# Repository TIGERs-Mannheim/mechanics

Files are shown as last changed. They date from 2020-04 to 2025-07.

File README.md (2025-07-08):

# TIGERs Mannheim Open-Source Mechanics

This repository contains mechanics for our robots and our base station. There is one folder for each released version.  
Mechanics are designed with: 
 - [Autodesk Inventor Professional 2019](https://www.autodesk.com/education/free-software/inventor-professional) (v2020) 
 - [Autodesk Inventor Professional 2022](https://www.autodesk.com/education/free-software/inventor-professional) (v2022) 
 - [Autodesk Inventor Professional 2023](https://www.autodesk.com/education/free-software/inventor-professional) (v2023, v2024, v2025) 
 
Autodesk Inventor is available for free for students.

Have a look at our [2020 ETDP](https://tigers-mannheim.de/download/tdps/2020_ETDP_TIGERS.pdf) and [2020 Champion Paper](https://download.tigers-mannheim.de/papers/2021-RoboCup-Champion.pdf) which contain many details about design decisions and lessons learned over more than 10 years.

Please check subfolders for further information on each version.

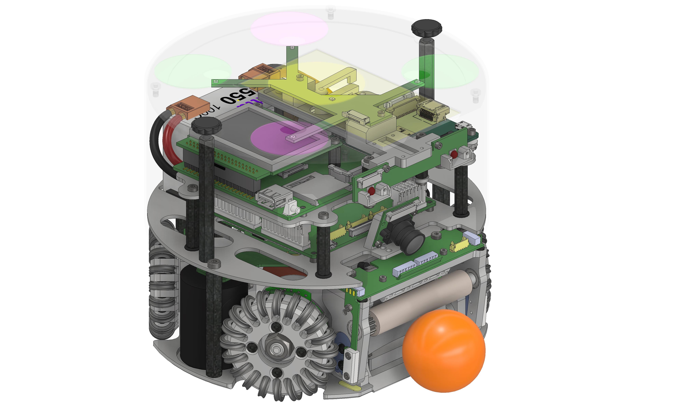
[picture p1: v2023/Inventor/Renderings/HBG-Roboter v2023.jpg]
v2023 Robot


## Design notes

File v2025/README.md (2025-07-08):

# v2025 Mechanics

Compared to the v2024 release the following changes have been made:
- The robot case for the black and white hull requirement has been redesigned
- The rear and side dribbler dampers have been updated in shape
- Camera and ball sensor arrays have been removed

Inventor folder contains the complete Inventor project for robot and base station including all parts.

STEP folder contains full step files of the robot assembly and the base station assembly. These files should be compatible with most CAD programs.

The `Purchased Parts.xlsx` file lists all third-party components used in the robot, including quantities, online shop URL and order number.  

## Electronic boards
v2025 robots use the following electronics boards which can be found in the electronics open-source repo:
- Ball Detection v4 (Break beam sensor)
- Encoder iC-PX v1b (Encoder IC carrier board)
- Front LEDs v1b
- IR Controller v2 (Break beam processor)
- Kicking Device v13b (Capacitor charge/discharge board)
- Mainboard v13 (Primary microcontroller and wireless transmitter board)
- Pattern Ident v2 (Automatic pattern identification system)
- Powerboard v1 (High current power board, motor controllers and power distribution)

## Inventor
To make sure all parts can be found by Inventor open the corresponding project file under `Inventor/TIGERs 2025.ipj`.  
The primary assembly file for the robot is `Inventor/Robot/HBG-Roboter v2025.iam`. You can open sub-assemblies by right-clicking on them and select open.  
The primary assembly file for the base station is `Inventor/Base Station/HBG-Base Station v3.iam`.

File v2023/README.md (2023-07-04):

# v2023 Mechanics

Compared to the v2022 release changes have been made to the dribbler dampening mechanism. Furthermore, dampers and dribbling bar are now 3D printed and part of the STL files. The sub-wheel axes of all wheels have been changed to better fit in the main wheel pockets.

Inventor folder contains the complete Inventor project for robot and base station including all parts.

PDF folder contains manufacturing drawings for parts produced by milling or turning. Note that only outer dimensions and important tolerances are given. Other data must be taken from STEP files.

STEP folder contains STEP files for manufacturing of parts produced by milling and turning as well as a file for the whole assembly of the robot.

STL folder contains all parts manufactured by 3D printing. See subfolder for material recommendations.

## Electronic boards
v2023 robots use the following electronics boards which can be found in the electronics open-source repo:
- Ball Detection v4 (Break beam sensor)
- Encoder iC-PX v1b (Encoder IC carrier board)
- Front LEDs v1b
- IR Controller v2 (Additional ball sensor and break beam processor)
- Kicking Device v13b (Capacitor charge/discharge board)
- Mainboard v13 (Primary microcontroller and wireless transmitter board)
- Pattern Ident v2 (Automatic pattern identification system)
- Powerboard v1 (High current power board, motor controllers and power distribution)

## Inventor
To make sure all parts can be found by Inventor open the corresponding project file under `Inventor/TIGERs 2023.ipj`.  
The primary assembly file for the robot is `Inventor/Robot/HBG-Roboter v2023.iam`. You can open sub-assemblies by right-clicking on them and select open.  
The primary assembly file for the base station is `Inventor/Base Station/HBG-Base Station v3.iam`.  
The excel list at `Inventor/Purchased Parts.xlsx` contains all purchased parts, including quantities, online shop URL and order number.  
Some image renderings are available at `Inventor/Renderings`.  
Inventor presentation files and drawings are in `Inventor/Presentations` and `Inventor/Drawings`, respectively.

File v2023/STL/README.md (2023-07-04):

# 3D Printed-Parts

All parts have been successfully printed on a Prusa i3 MK3S printer with a standard 0.4mm nozzle.
File names correspond to Inventor part names.

### Base Station v3
Recommended materials and layer heights for each part:

| Part | Material | Layer Height |
| --- | --- | --- |
| Base Station v3 | PLA | 0.2mm |

### Robot
Recommended materials and layer heights for each part:

| Part | Material | Layer Height |
| --- | --- | --- |
| Akkuhalter | PLA | 0.2mm |
| Akkusperre | PETG | 0.2mm |
| Akkusperre Klein | PETG | 0.2mm |
| Ballsensor Platinenwinkel | PLA | 0.1mm |
| Ballsensormaske | PLA | 0.1mm |
| Chipanschlag L2.0 | TPU98 | 0.1mm |
| Displayhalter Bot | PLA | 0.2mm |
| Dribbler Slider | Recreus FilaFlex 70A | 0.2mm |
| Dribbler Slider gespiegelt | Recreus FilaFlex 70A | 0.2mm |
| Dribblerschnecke v2 | Recreus FilaFlex 70A | 0.2mm |
| Dribblerdaempfer v2 | Recreus FilaFlex 70A | 0.2mm |
| Gehäuse Mantel | PETG | 0.3mm |
| Gehäuse Unterplatte | PLA | 0.2mm |
| IR Schutz | PLA | 0.2mm |
| Kamerahalter Vorne geneight | PLA | 0.2mm |
| Kameraplatte | PLA | 0.2mm |
| Kickerboard Winkel | PLA | 0.2mm |
| Kickerdaempfer | TPU98 | 0.2mm |
| LED Schirm | PETG | 0.2mm |
| Spulenkörper | PLA | 0.2mm |

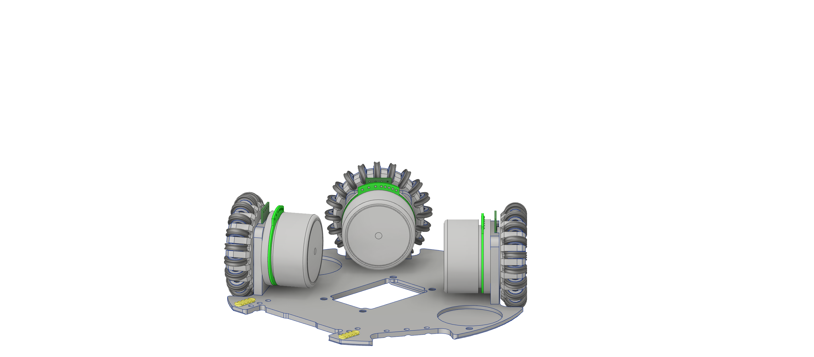
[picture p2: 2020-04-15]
v2020/Inventor/Renderings/HBG-Roboter v2020-5.png

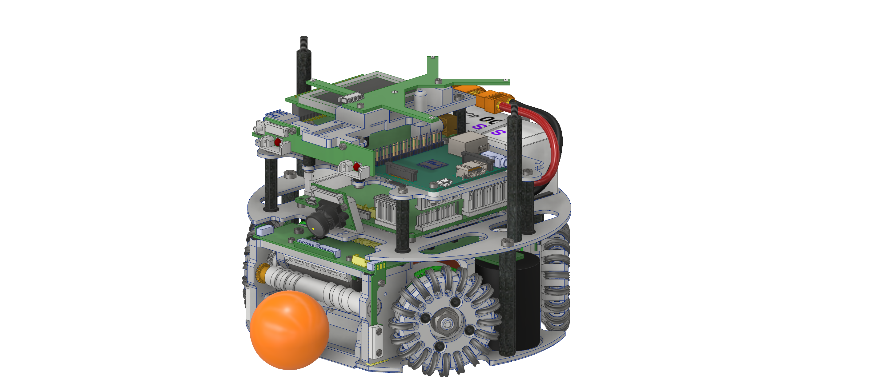
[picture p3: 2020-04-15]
v2020/Inventor/Renderings/HBG-Roboter v2020-1.png

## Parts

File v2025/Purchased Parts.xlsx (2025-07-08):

Quantity | Part | Description | Supplier | Part Number
8 | ISO 1580 M2 x 3 | Flachkopfschraube mit Schlitz, rostfrei | wegertseder.de | 1094-002
4 | DIN 84 - M3 x 6 | Zylinderschraube, polyamid schwarz | wegertseder.de | 3989-300
4 | ISO 4762 - M2 x 4 | Zylinderschraube | wegertseder.de | 2534-230
34 | ISO 4762 - M2 x 6 | Zylinderschraube | wegertseder.de | 2534-234
4 | ISO 4762 - M2,5 x 10 | Zylinderschraube | wegertseder.de | 2534-258
28 | DIN 7984 - M3 x 5 | Zylinderschraube, rostfrei | wegertseder.de | 2594-928
10 | DIN 7984 - M4 x 6 | Zylinderschraube, niedriger Kopf | wegertseder.de | 2594-954
20 | ISO 10642 - M3 x 6 | Senkschraube mit Innensechskant | wegertseder.de | 2608-680
42 | ISO 10642 - M3 x 8 | Senkschraube mit Innensechskant | wegertseder.de | 2608-682
8 | ISO 10642 - M4 x 8 | Senkschraube mit Innensechskant | wegertseder.de | 2608-708
2 | DIN 467 - M4 | Rändelmutter M4 | wegertseder.de | 2058-782
4 | DIN 934 - M2,5 | Sechskantmuttern, M2.5 | wegertseder.de | 2896-142
4 | DIN 934 - M8 | Sechskantmuttern, Alu, M8 | wegertseder.de | 2914-422
4 | DIN 562 M3 | Vierkantmutter, niedrige Form, M3 | wegertseder.de | 3198-486
0 | DIN 125 A3.2 | Unterlegscheibe, polyamid | wegertseder.de | 1504-436
0 | DIN 125 A5.3 | Unterlegscheibe, polyamid | wegertseder.de | 1504-440
4 | DIN 137 B8 | Federscheibe Form B, 8mm, Federstahl, verzinkt | wegertseder.de | 1738-294
10 | ISO 2338 - 2 m6 x 4 | Zylinderstift m6 2x4 | wegertseder.de | 4347-136
80 | ISO 2338 - 2 m6 x 6 | Zylinderstift m6 2x6 | wegertseder.de | 4347-140
1 | ISO 2338 - 2 m6 x 16 | Zylinderstift m6 2x16 | wegertseder.de | 4347-150
0 | DIN 988 4 x 8 x 0,2 | Passscheibe M4, 0.2mm | wegertseder.de | 1652-940
4 | DIN EN ISO 8745 4 x 10 | Paßkerbstift 4x10 | wegertseder.de | 1028-042
1 | Moons ECU22048H18 | Moons ECU22048H18, 55W, 18V, Slotless BLDC Motor | moonsindustries.com | ECU22048H18-S101
4 | DF45L024048-A2 | Motor Nanotec, 65Watt, 24V | nanotec.de | DF45L024048-A2
4 | iC-PX2604 | iC-PX2604 oDFN8-3x3 Reflective Encoder, 23040cpr | ichaus.de | iC-PX2604
4 | PX01FS | PX01FS 26-360 Code Disc, 360, selbstklebend | ichaus.de | PX01FS 26-360
1 | Akku 6S1P Tattu | Tattu Funfly 1550mAh 22,2V 100C | gensace.de | TAA15506S10X6
1 | XT Akku Anschluss | XT60 Stecker | stefansliposhop.de | SLS XT-60 Stecker SK
1 | Charge Marker | Charge Marker | stefansliposhop.de | C-Marker
2 | Kugellager 685-ZZ-C3 | Kugellager, beidseitig Deckscheiben, ID=5, AD=11, b=5 | kugellager-express.de | 685-ZZ-C3
2 | Kugellager 683-ZZ | Kugellager, beidseitig Deckscheiben, ID=3, AD=7, b=3 | kugellager-express.de | 683-ZZ
2 | Zahnrad z14 Modul 0.7 | Stirnzahnrad, Stahl, Modul 0.7, z=14 | maedler.de | 21201400
1 | Zahnrad Polyketon z16 Modul 0.7 | Stirnzahnrad, Polyketon, Modul 0.7, z=16 | maedler.de | 28201601
80 | X-Ring, 5.94x3.53 | X-Ring, 5.94x3.53mm, NBR, Shore A 70 | ir-dichtungstechnik.de | XRINGBS202NBR70
160 | Gleitlager MSM-0205-02 | Gleitlager Querrolle MSM-0205-02 | igus.de | JSM-1012-05
4 | Zugfeder Z-015LI | Zugfeder Z-015LI, Kicker | federnshop.com | Z-015LI
2 | Zugfeder RZ-006DI | Zugfeder RZ-006DI, Chip Schaufel | federnshop.com | RZ-006DI
4 | M4x60 | Abstandsbolzen Typ A, M4, 60mm, Kunststoff | ettinger.de | 5.30.460
2 | M4x70 | Abstandsbolzen Typ B, M4, 70mm, Stahl | ettinger.de | 5.14.701
4 | M3x30 | Abstandsbolzen Typ A, M3, 30mm, Kunststoff | ettinger.de | 5.30.330
3 | M3x20 | Abstandsbolzen Typ A, M3, 20mm, Kunststoff | ettinger.de | 5.30.320
28 | Kupferlackdraht 140m | Kupferlackdraht (Spule) 0.63mm, 6-7 Lagen | conrad.de | 605523
 |  | Doppelseitiges Klebeband, schneidbar | conrad.de | 542373
8 |  | Gummitülle 3mm | digikey.de | 1722-1291-ND
4 |  | Distanzhülse 3mm M2.5 (RPi) | digikey.de | 952-1526-ND
2 |  | Abstandsbolzen Kunststoff (Mainboard), 12mm | digikey.de | 952-3457-ND
 | Loctite | Wellensicherungskleber im Spenderstift | de.rs-online.com | 476-7870

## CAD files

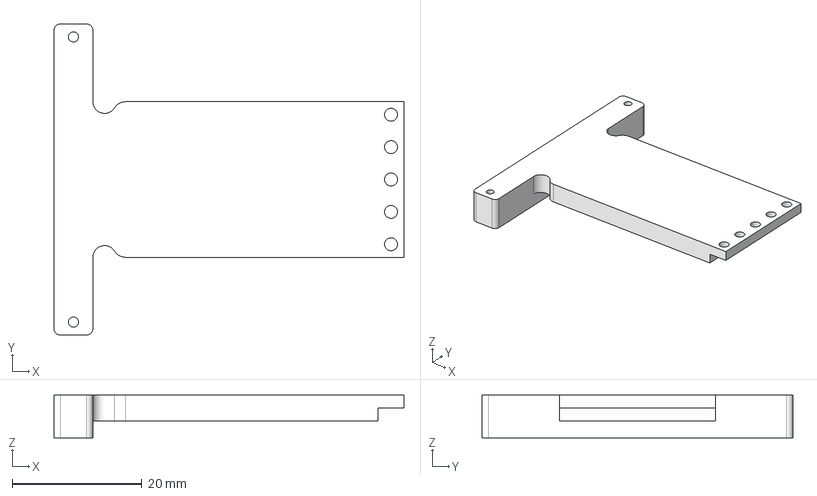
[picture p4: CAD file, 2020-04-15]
v2020/STEP/32_Kicker Chip.ipt.step
54.0 x 48.0 x 6.60 mm

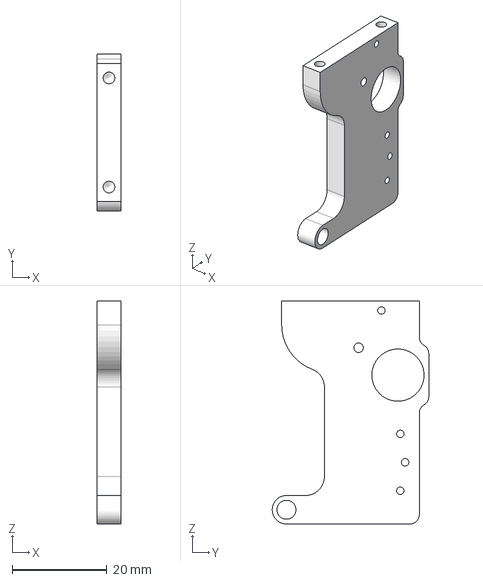
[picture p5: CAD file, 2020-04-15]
v2022/STEP/21_Dribbler Seite.ipt.step
5.00 x 33.0 x 47.0 mm

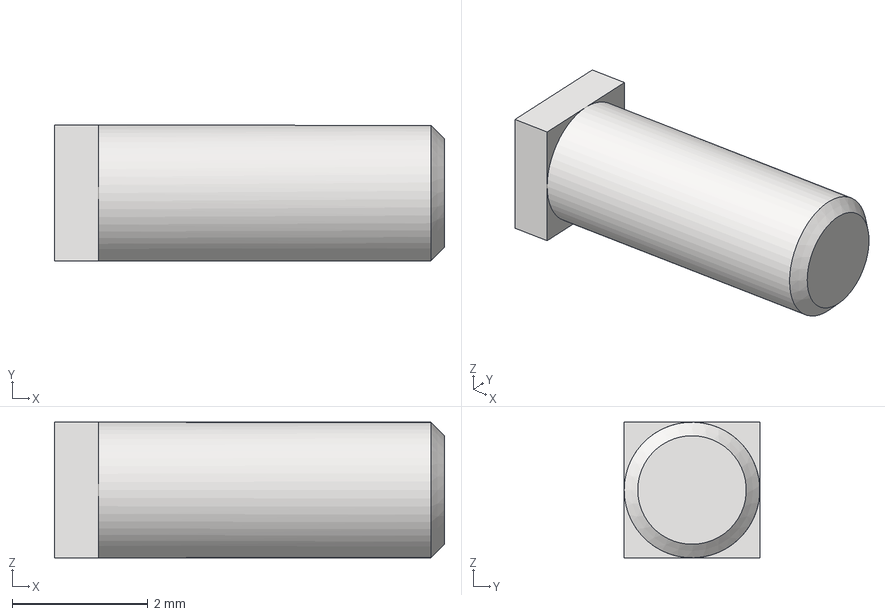
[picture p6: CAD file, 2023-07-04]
v2023/STEP/16_Welle Querrolle Quad.stp
5.75 x 2.00 x 2.00 mm

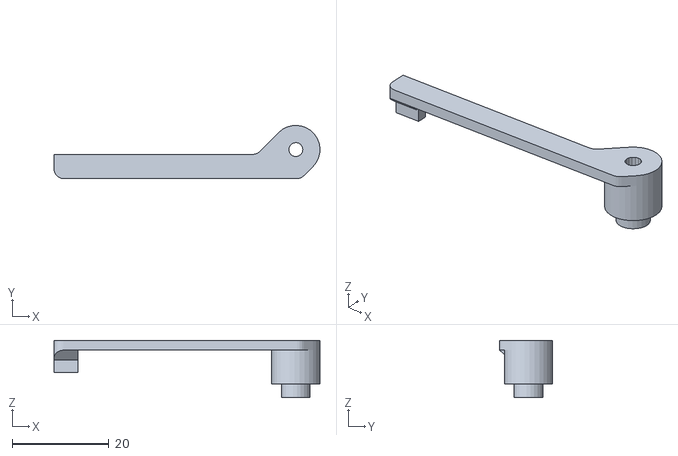
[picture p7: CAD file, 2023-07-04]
v2023/STL/Robot/Akkusperre.stl
55.0 x 11.0 x 11.8

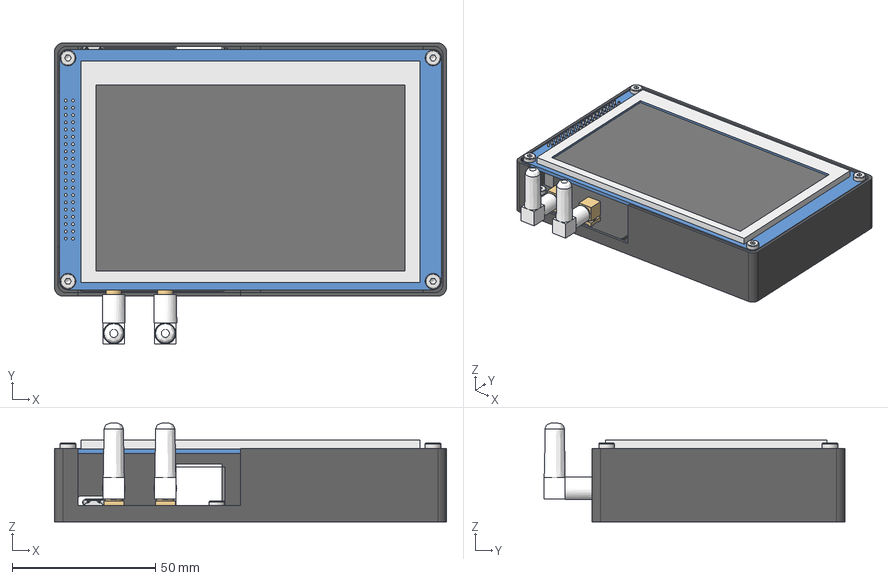
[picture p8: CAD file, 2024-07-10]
v2025/STEP/HBG-Base Station v3.stp
136.9 x 105.1 x 34.4 mm
Gehaeuse BS v3
Base Station PCB
RJ45 Socket
Antenne-Klein x 2
SMA-F-RA x 2
ESQ-120-33-T-D_socket
ESQ-120-33-T-D_pins
ESQ-120-33-G-D-LL_bpins
TFT-CP11009
DIN 7984 - M3 x 5 x 7

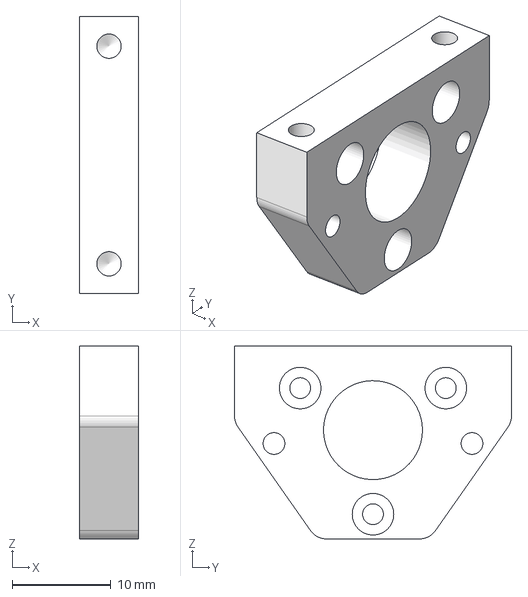
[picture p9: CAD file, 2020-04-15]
v2020/STEP/25_Motorhalter.ipt.step
6.00 x 28.0 x 19.5 mm

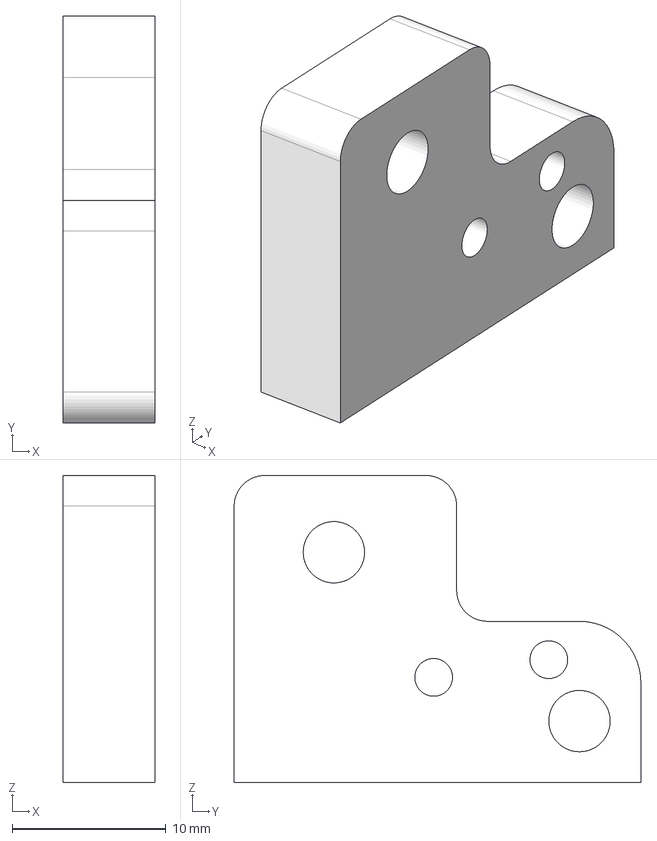
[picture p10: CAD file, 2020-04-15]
v2022/STEP/20_Dribbler Lagerbock.ipt.step
6.00 x 26.5 x 20.0 mm

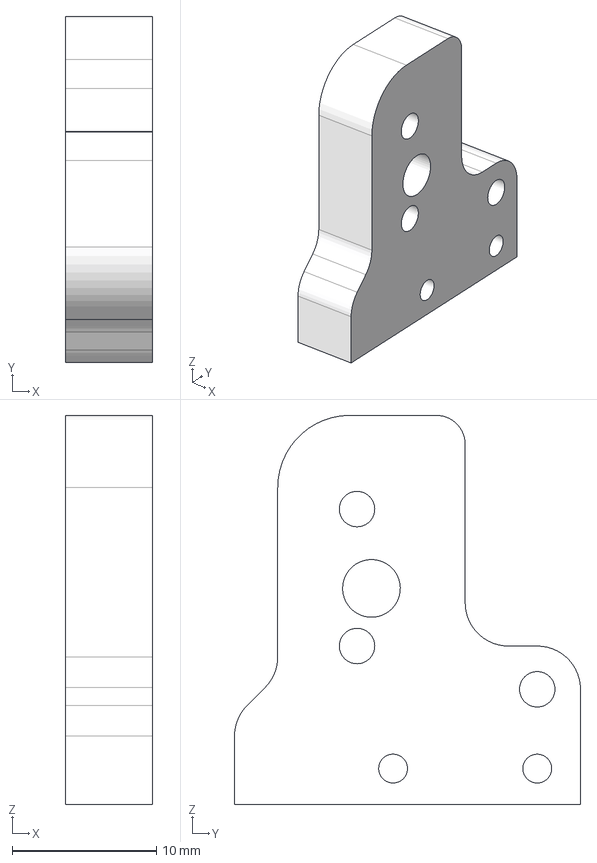
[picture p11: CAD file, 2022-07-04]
v2023/STEP/26D_Dribbler Lagerbock v2.ipt.step
6.00 x 24.0 x 27.0 mm

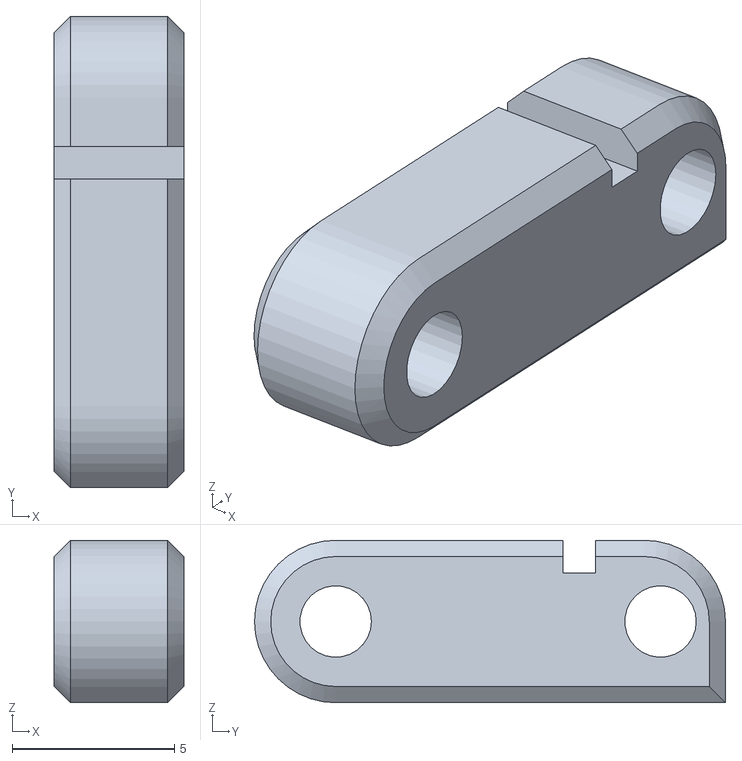
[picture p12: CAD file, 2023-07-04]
v2023/STL/Robot/Chipanschlag L2.0.stl
4.00 x 14.5 x 5.00

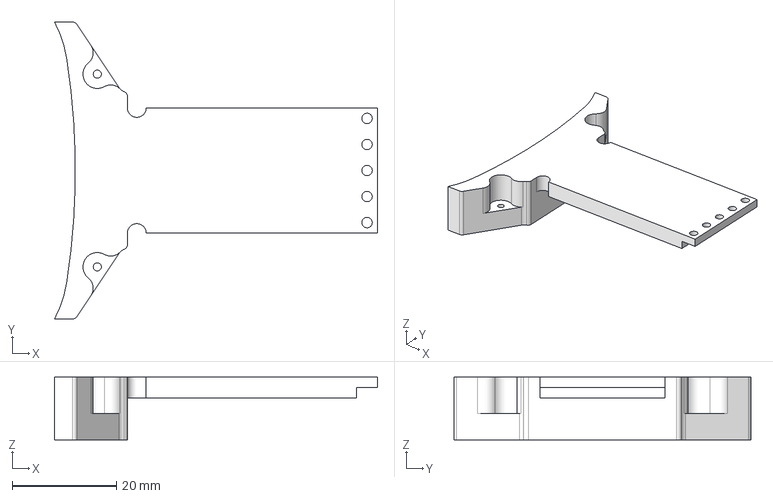
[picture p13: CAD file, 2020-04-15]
v2020/STEP/31_Kicker Sichel.ipt.step
62.0 x 57.0 x 12.0 mm

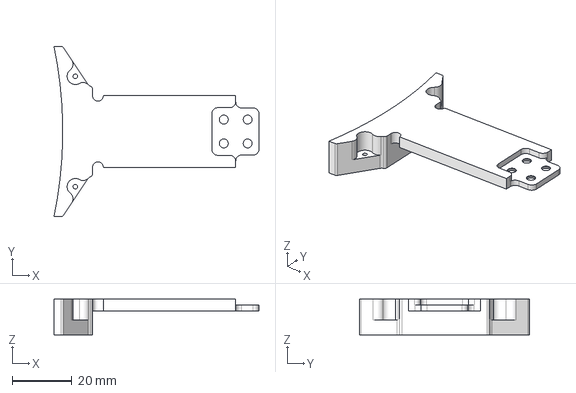
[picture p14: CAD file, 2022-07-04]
v2023/STEP/31B_Kicker Sichel.ipt.step
68.7 x 57.0 x 12.0 mm

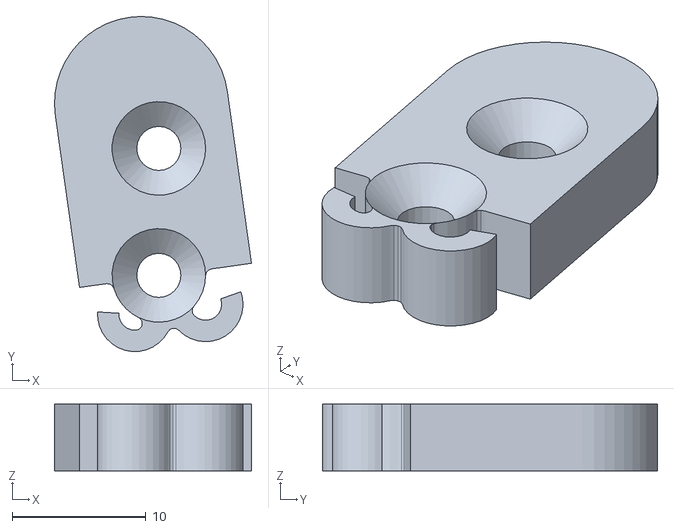
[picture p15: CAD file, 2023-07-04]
v2023/STL/Robot/Dribbler Slider.stl
14.7 x 25.1 x 5.00

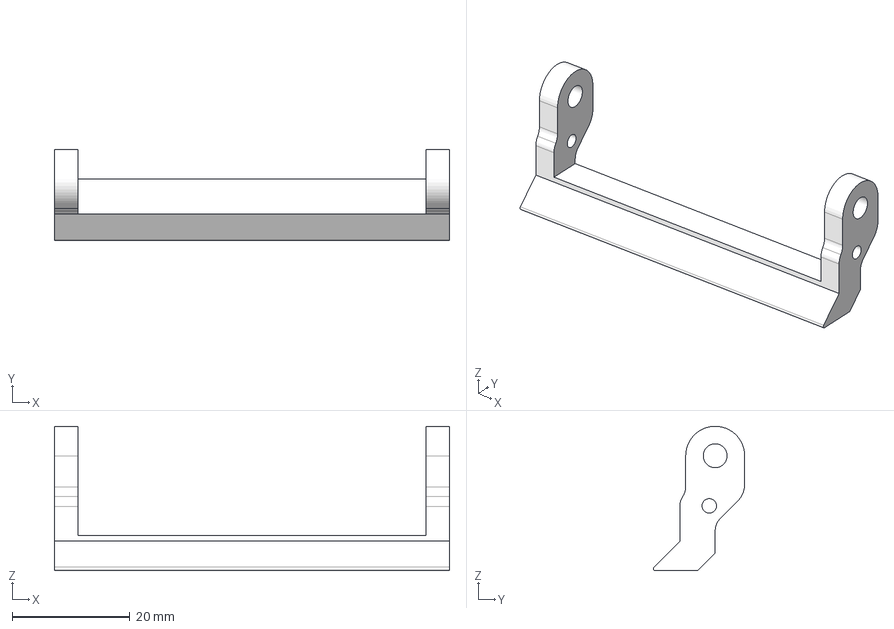
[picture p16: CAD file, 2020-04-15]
v2020/STEP/23_Chip Schaufel.ipt.step
67.0 x 15.5 x 24.5 mm

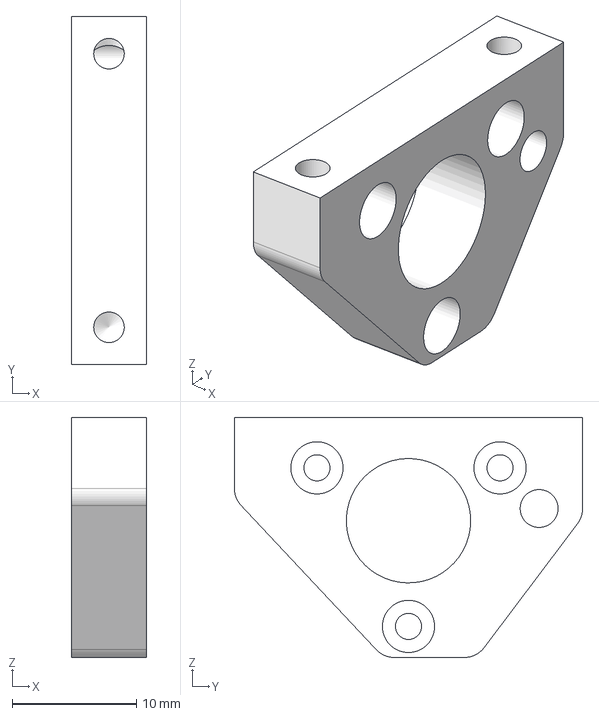
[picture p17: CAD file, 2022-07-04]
v2023/STEP/25D_Motorhalter.ipt.step
6.00 x 28.0 x 19.3 mm

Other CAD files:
v2023/STL/Robot/Akkusperre Klein.stl
v2020/STEP/30_Kicker Eisen.ipt.step
v2023/STEP/30B_Kicker Eisen.ipt.step
v2023/STL/Robot/Dribblerschnecke v2.stl
v2020/Inventor/Base Station/Base Station PCB.ipt
v2020/Inventor/Base Station/Gehaeuse BS v3.ipt
v2020/Inventor/Base Station/HBG-Base Station v3.iam
v2020/Inventor/Base Station/MG-Base Station PCB.iam
v2020/Inventor/Base Station/UBG-Electronics.iam
v2020/Inventor/Drawings/01_Grundplatte.idw
v2020/Inventor/Drawings/02_Mittelplatte.idw
v2020/Inventor/Drawings/03_Oberplatte.idw
v2020/Inventor/Drawings/10_Lagerbock.idw
v2020/Inventor/Drawings/11_Radadapter.idw
v2020/Inventor/Drawings/12_Radkasten.idw
v2020/Inventor/Drawings/13_Raddeckel.idw
v2020/Inventor/Drawings/14_Rolle.idw
v2020/Inventor/Drawings/20_Dribbler Lagerbock.idw
v2020/Inventor/Drawings/21_Dribbler Seite.idw
v2020/Inventor/Drawings/22_Dribbler Bruecke.idw
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

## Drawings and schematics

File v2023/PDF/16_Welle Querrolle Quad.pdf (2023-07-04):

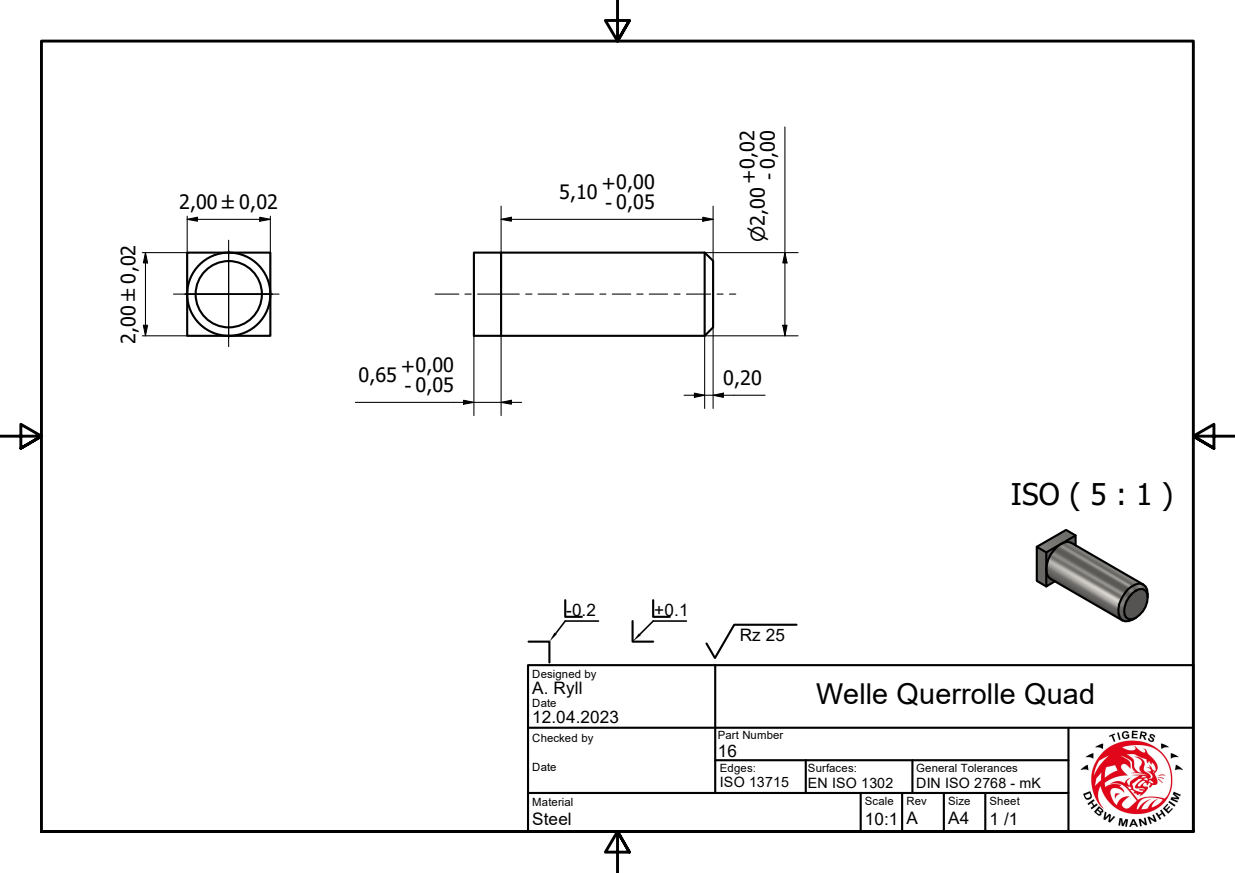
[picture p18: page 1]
ISO ( 5 : 1 )

Designed by A. Ryll Date 12.04.2023 | Welle Querrolle Quad

Checked by Date | Part Number 16

Edges: ISO 13715 | Surfaces: EN ISO 1302 | General Tolerances DIN ISO 2768 - mK

Material Steel | Scale 10:1 | Rev A | Size A4 | Sheet 1 /1

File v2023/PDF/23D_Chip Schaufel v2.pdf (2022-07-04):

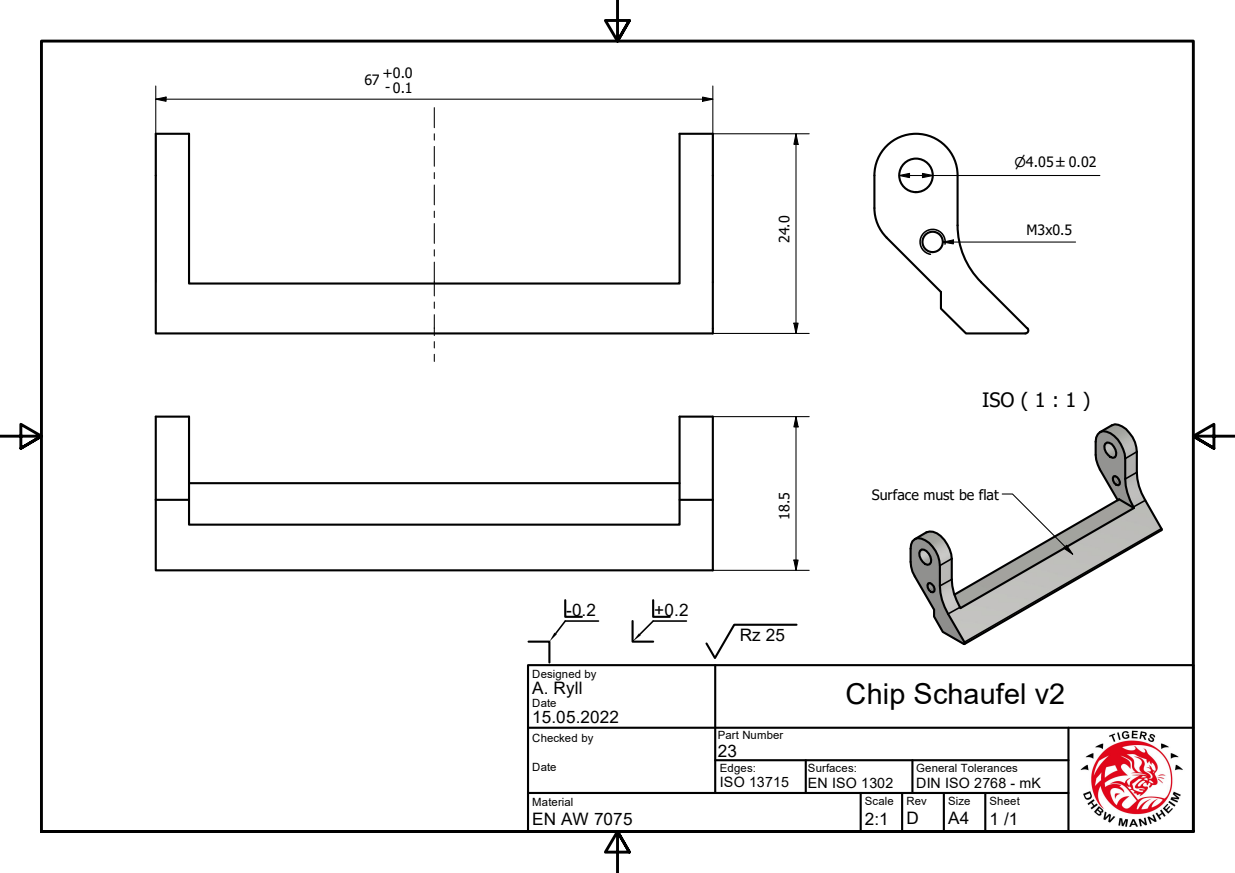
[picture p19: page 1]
ISO ( 1 : 1 )

Surface must be flat

Designed by A. Ryll Date 15.05.2022 | Chip Schaufel v2

Checked by Date | Part Number 23

Edges: ISO 13715 | Surfaces: EN ISO 1302 | General Tolerances DIN ISO 2768 - mK

Material EN AW 7075 | Scale 2:1 | Rev D | Size A4 | Sheet 1 /1

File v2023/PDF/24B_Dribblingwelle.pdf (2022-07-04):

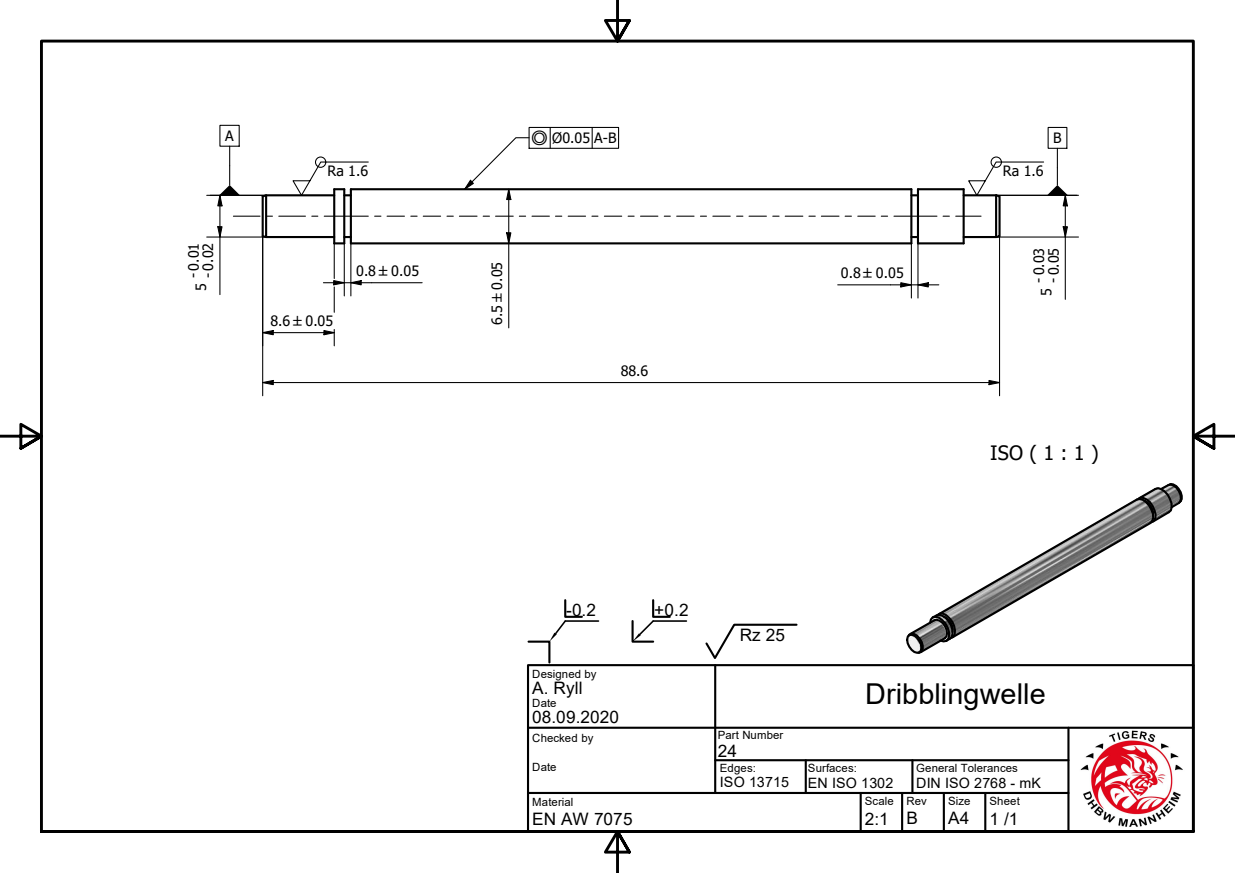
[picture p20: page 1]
ISO ( 1 : 1 )

Designed by A. Ryll Date 08.09.2020 | Dribblingwelle

Checked by Date | Part Number 24

Edges: ISO 13715 | Surfaces: EN ISO 1302 | General Tolerances DIN ISO 2768 - mK

Material EN AW 7075 | Scale 2:1 | Rev B | Size A4 | Sheet 1 /1

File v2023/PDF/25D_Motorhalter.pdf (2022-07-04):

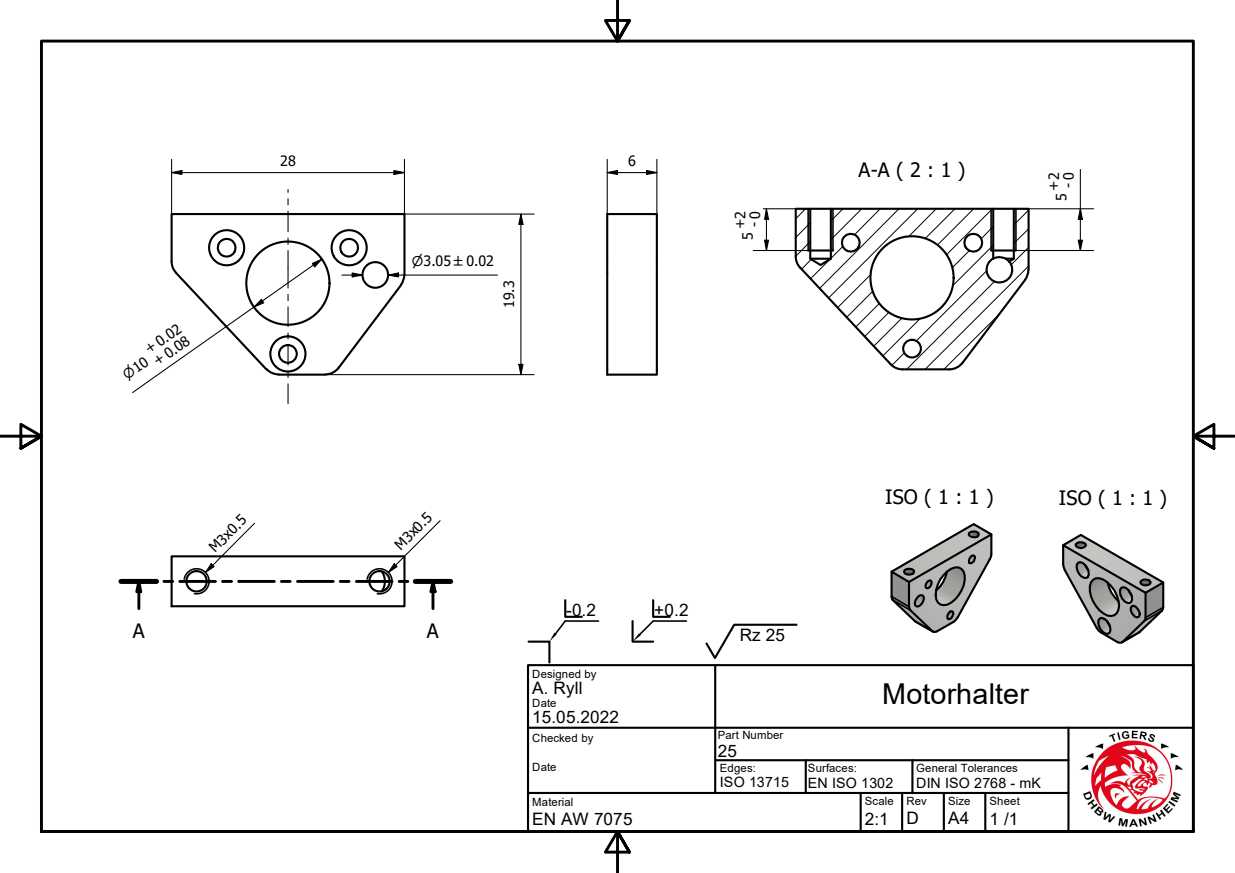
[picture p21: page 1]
ISO ( 1 : 1 )

Designed by A. Ryll Date 15.05.2022 | Motorhalter

Checked by Date | Part Number 25

Edges: ISO 13715 | Surfaces: EN ISO 1302 | General Tolerances DIN ISO 2768 - mK

Material EN AW 7075 | Scale 2:1 | Rev D | Size A4 | Sheet 1 /1

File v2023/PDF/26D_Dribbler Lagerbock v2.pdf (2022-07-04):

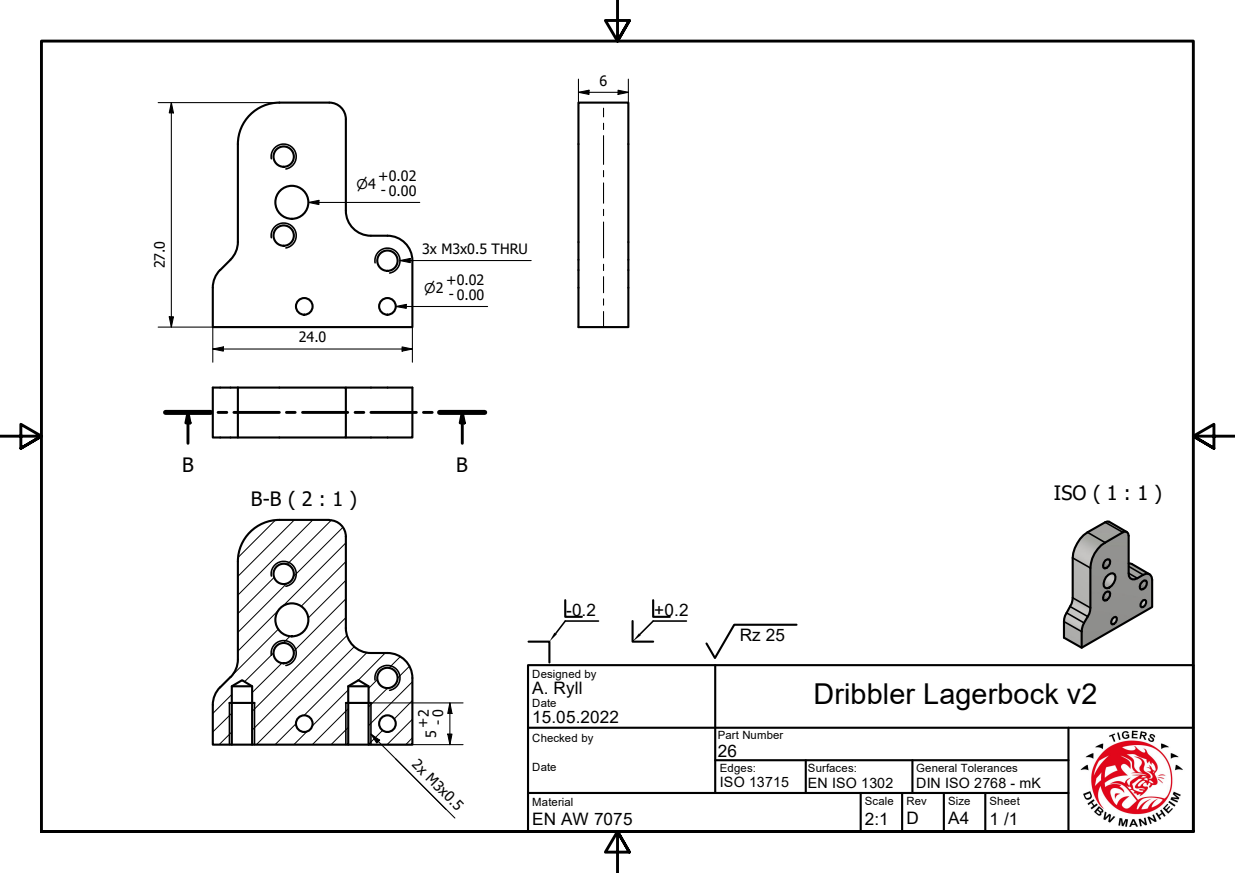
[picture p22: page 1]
ISO ( 1 : 1 ) B-B ( 2 : 1 ); 3x M3x0.5 THRU

Designed by A. Ryll Date 15.05.2022 | Dribbler Lagerbock v2

Checked by Date | Part Number 26

Edges: ISO 13715 | Surfaces: EN ISO 1302 | General Tolerances DIN ISO 2768 - mK

Material EN AW 7075 | Scale 2:1 | Rev D | Size A4 | Sheet 1 /1

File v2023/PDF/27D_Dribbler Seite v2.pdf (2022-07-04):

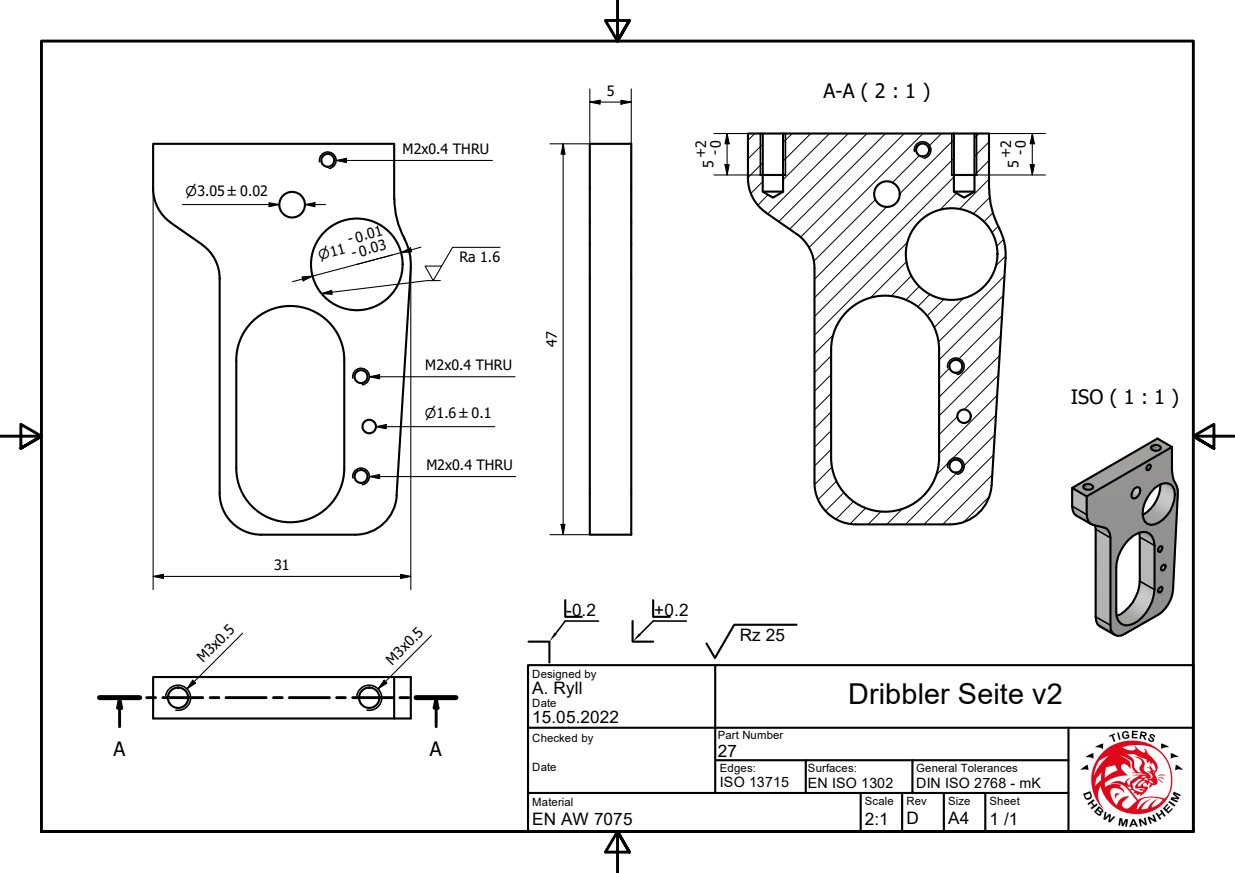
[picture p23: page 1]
ISO ( 1 : 1 ); M2x0.4 THRU

Designed by A. Ryll Date 15.05.2022 | Dribbler Seite v2

Checked by Date | Part Number 27

Edges: ISO 13715 | Surfaces: EN ISO 1302 | General Tolerances DIN ISO 2768 - mK

Material EN AW 7075 | Scale 2:1 | Rev D | Size A4 | Sheet 1 /1

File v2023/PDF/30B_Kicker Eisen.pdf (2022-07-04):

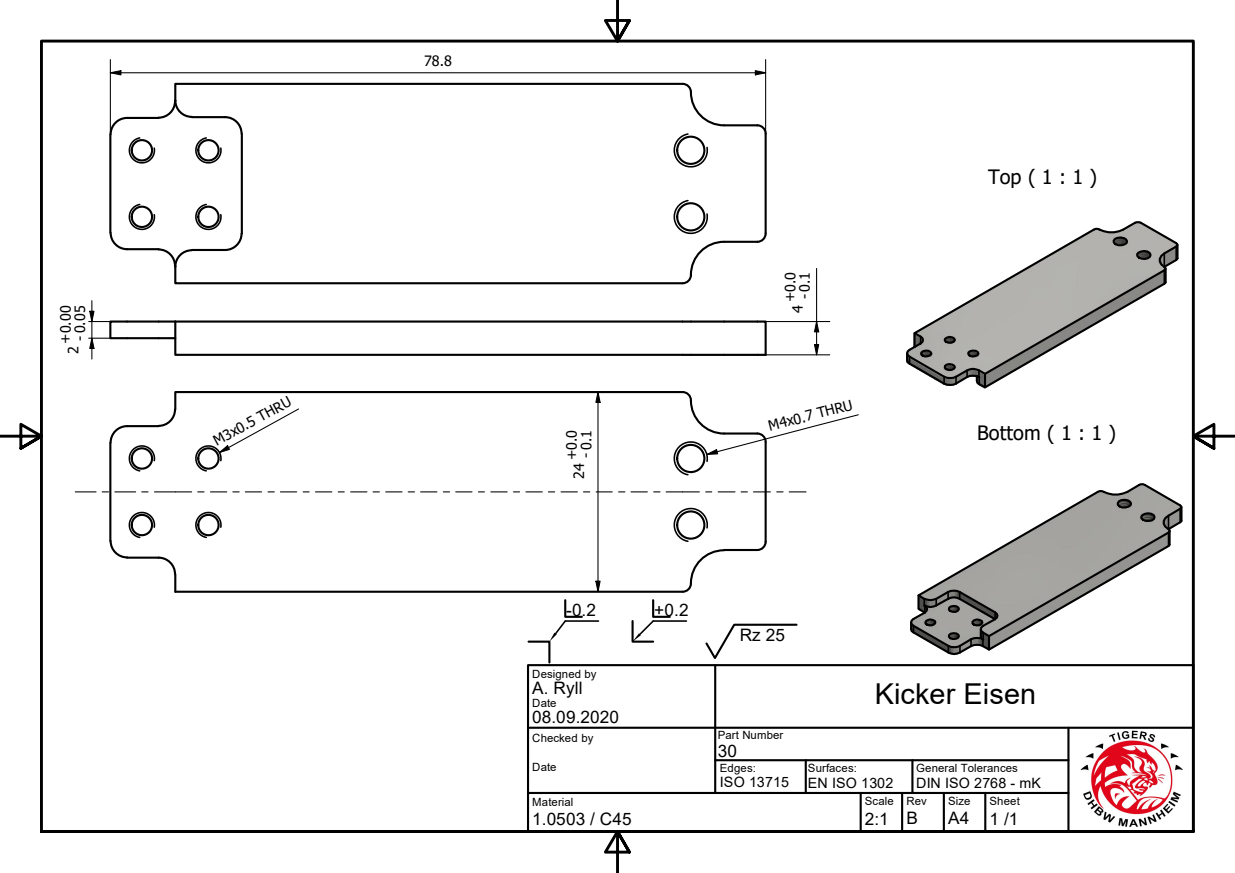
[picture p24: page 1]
Top ( 1 : 1 ); Bottom ( 1 : 1 ); M4x0.7 THRU; M3x0.5 THRU

Designed by A. Ryll Date 08.09.2020 | Kicker Eisen

Checked by Date | Part Number 30

Edges: ISO 13715 | Surfaces: EN ISO 1302 | General Tolerances DIN ISO 2768 - mK

Material 1.0503 / C45 | Scale 2:1 | Rev B | Size A4 | Sheet 1 /1

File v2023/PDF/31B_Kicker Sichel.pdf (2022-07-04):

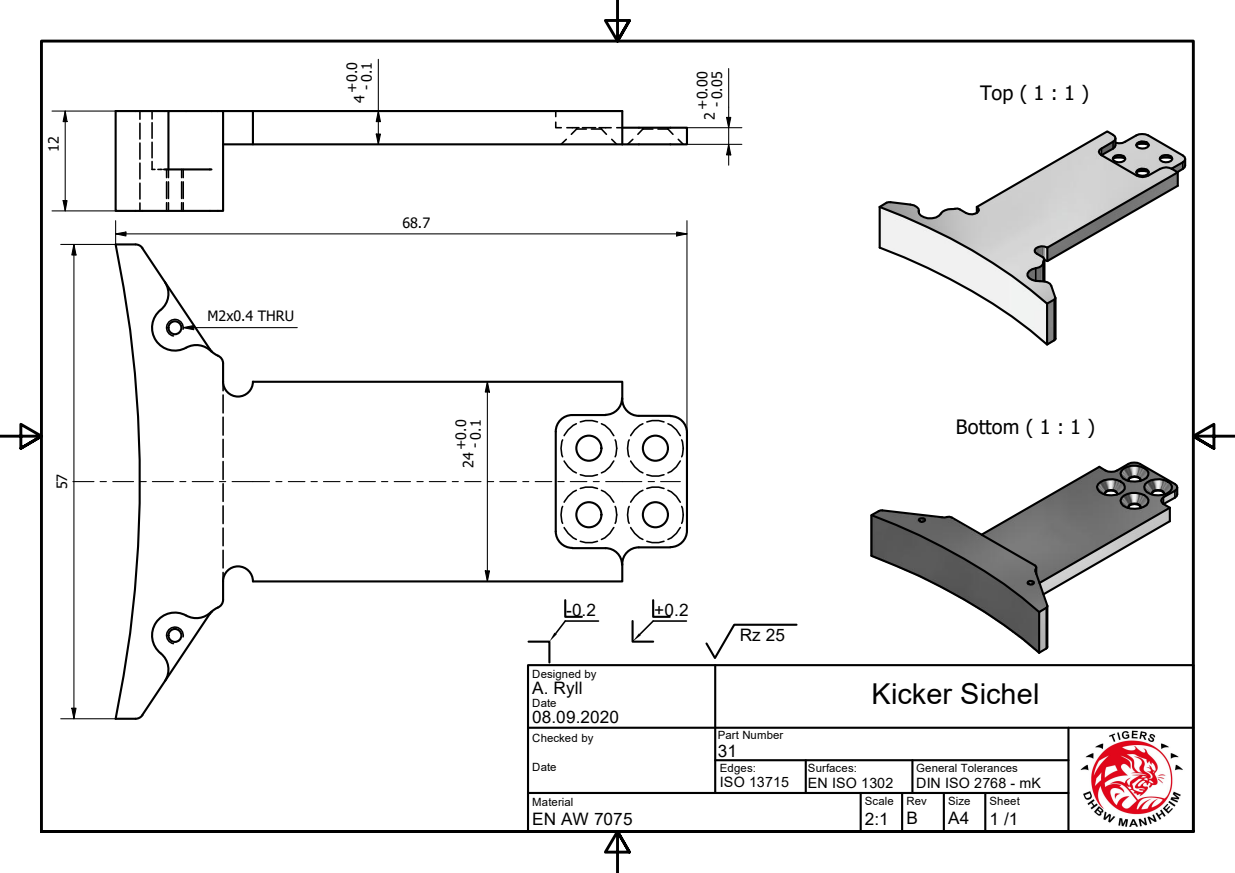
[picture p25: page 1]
Top ( 1 : 1 ); Bottom ( 1 : 1 ); M2x0.4 THRU

Designed by A. Ryll Date 08.09.2020 | Kicker Sichel

Checked by Date | Part Number 31

Edges: ISO 13715 | Surfaces: EN ISO 1302 | General Tolerances DIN ISO 2768 - mK

Material EN AW 7075 | Scale 2:1 | Rev B | Size A4 | Sheet 1 /1

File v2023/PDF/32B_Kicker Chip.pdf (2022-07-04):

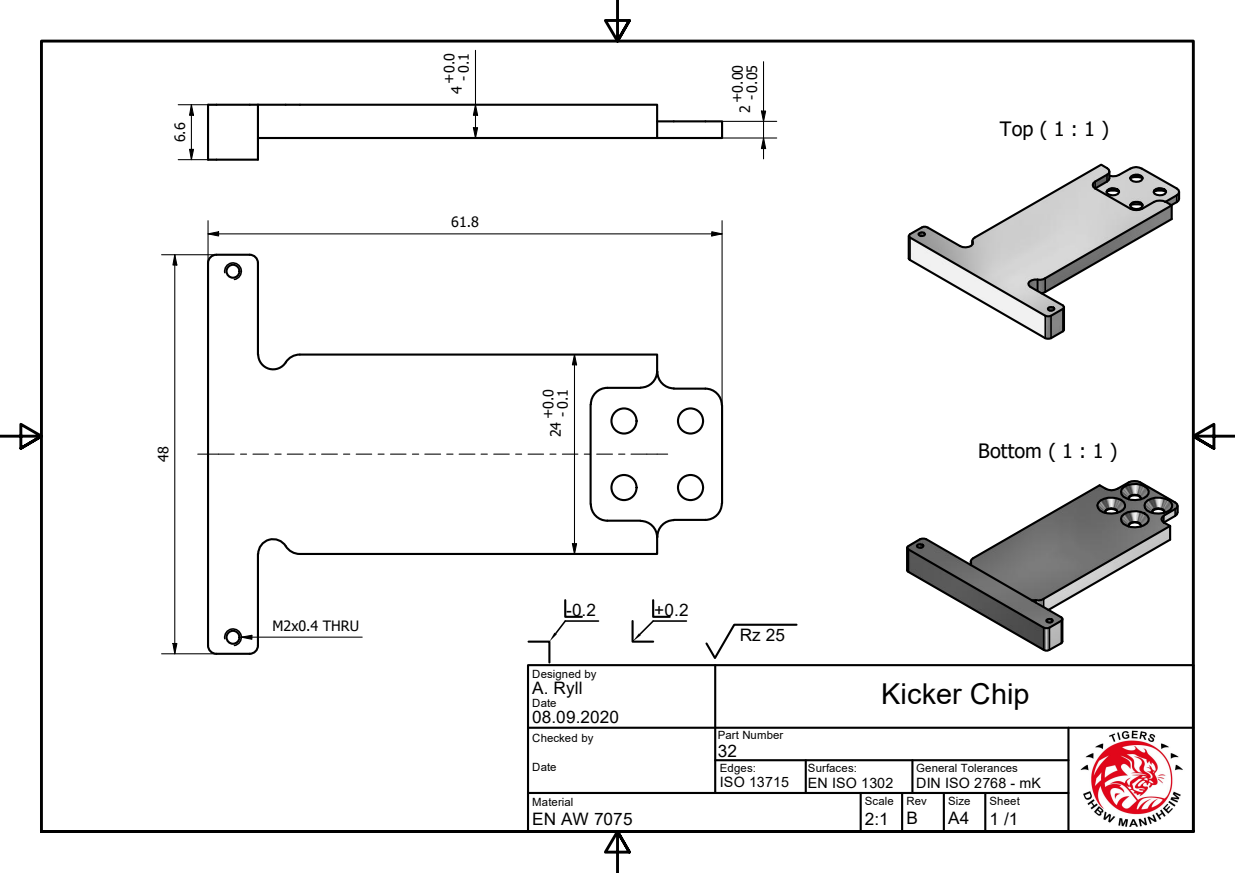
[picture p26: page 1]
Top ( 1 : 1 ); Bottom ( 1 : 1 ); M2x0.4 THRU

Designed by A. Ryll Date 08.09.2020 | Kicker Chip

Checked by Date | Part Number 32

Edges: ISO 13715 | Surfaces: EN ISO 1302 | General Tolerances DIN ISO 2768 - mK

Material EN AW 7075 | Scale 2:1 | Rev B | Size A4 | Sheet 1 /1

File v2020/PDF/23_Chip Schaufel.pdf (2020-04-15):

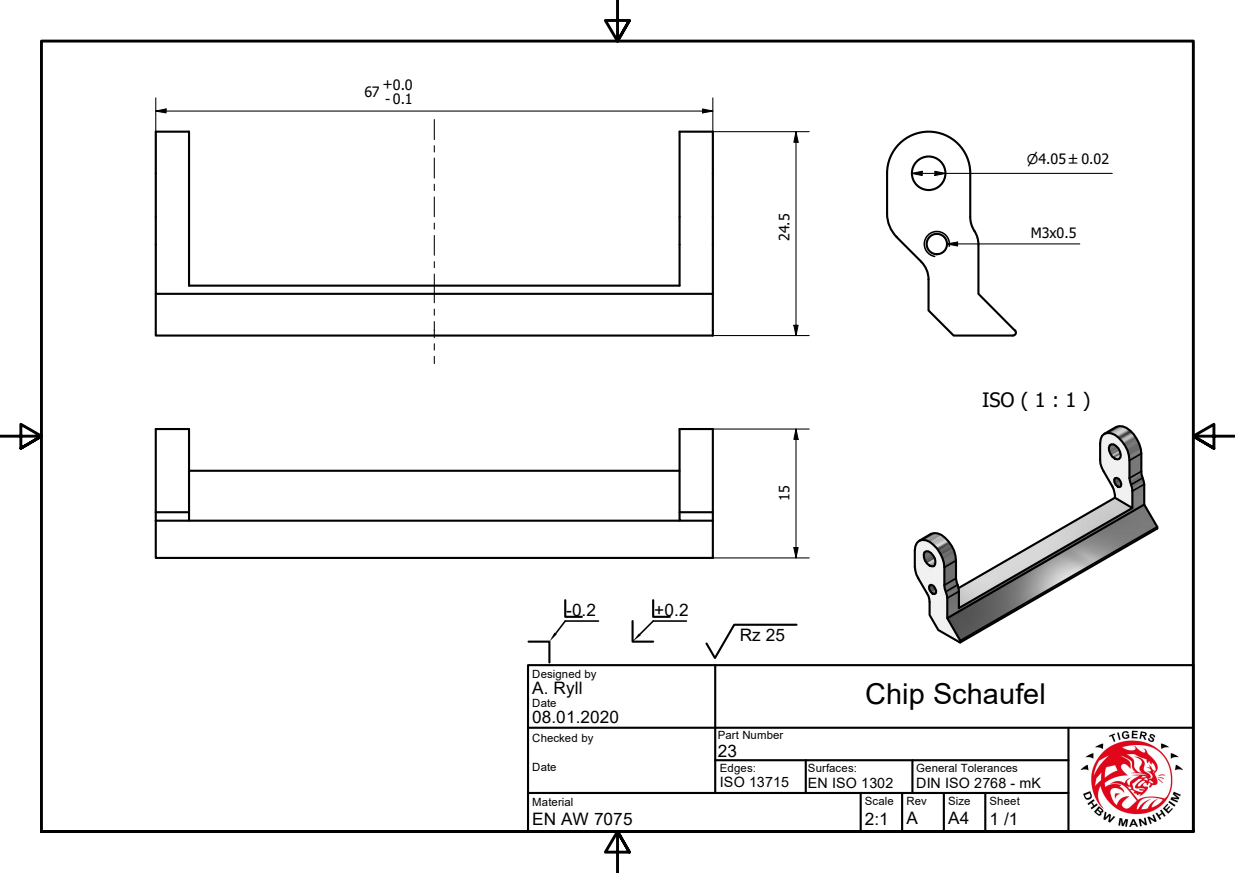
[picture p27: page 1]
ISO ( 1 : 1 )

Designed by A. Ryll Date 08.01.2020 | Chip Schaufel

Checked by Date | Part Number 23

Edges: ISO 13715 | Surfaces: EN ISO 1302 | General Tolerances DIN ISO 2768 - mK

Material EN AW 7075 | Scale 2:1 | Rev A | Size A4 | Sheet 1 /1

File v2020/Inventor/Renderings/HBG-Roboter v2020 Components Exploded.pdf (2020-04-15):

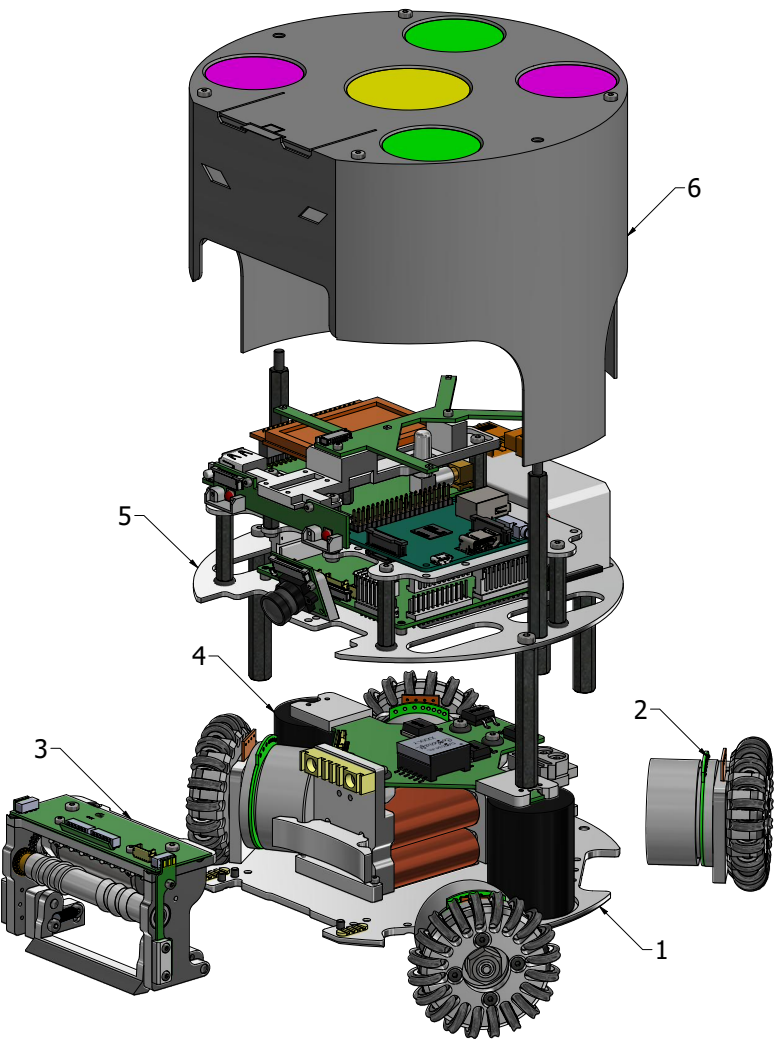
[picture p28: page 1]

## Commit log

2020-04-15 Open-Source release of v2020 mechanics
    [01_Grundplatte.idw, 01_Grundplatte.ipt.step, 02_Mittelplatte.idw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]
2020-04-17 Update README.md, v2020/README.md, v2020/STL/README.md files
2020-04-25 Added STEP file of the whole robot assembly
2022-07-04 v2022 mechanics release
    [01_Grundplatte.idw, 01_Grundplatte.ipt.step, 02_Mittelplatte.idw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]
2023-07-04 2023 Open-Source release
    [01_Grundplatte.idw, 01_Grundplatte.ipt.step, 02_Mittelplatte.idw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]
2023-07-04 Added v2023 debug display holder
    [Display 5inch Housing.ipt, Displayhalter Bot.ipt, MG-Display mit Housing.iam]
2024-07-10 2024 mechanics open-source release
    [AVX Interconnect 00-9155-003-541-006.ipt, AVX Interconnect 00-9155-006-741-006.ipt, Abstandsbolzen Typ A M3 20mm SW6.ipt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]
2025-07-08 2025 mechanics open-source release
    [AVX Interconnect 00-9155-003-541-006.ipt, AVX Interconnect 00-9155-006-741-006.ipt, Abstandsbolzen Typ A M3 20mm SW6.ipt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]
